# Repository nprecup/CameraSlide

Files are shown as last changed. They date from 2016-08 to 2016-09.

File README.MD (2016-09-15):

Automated Camera Slider
=================================================

The goal of this project is to create a budget, yet high quality, motorized camera slider, with two axis capability, and Bluetooth communications. This slider is to be used in very remote locations for time-lapse landscape astrophotography. This drives a requirement for portability, with a small battery and low power consumption.

Mechanical Design
-----------------------

The slide axis is made using two aluminum shafts that serve as rails. A low cost ACME lead screw moves the cart along the axis, driven by a low cost Futaba S3003 servo modified for continuous rotation. The controller can be adapted (without modification to the circuit) for other mechanical drive systems that may be more practical depending on the resources available, including belts or driven rollers. The choice of using hobby servos instead of stepper motors was made clear by the power consumption and complexity requirement. Complex motion profiles are not necessary, and open loop control will work fine. Stepper motors consume too much current, all the time (though the current can be reduced while not moving). Servo motors already have drivers built into them, making it necessary to supply only power and PWM control input. While the open loop control is based upon dead reckoning (timing), rather than by the advantageous simple steps of a stepper motor, the motors can be moved carefully to produce repeatable results. A stepper motor requires additional drive circuitry, increasing cost and complexity.

Circuit Design
-----------------------

This project uses a BlueGiga BLE112 module to control and interface with a motorized camera slide. The BLE112 module contains a 2541 microcontroller that is capable of providing 16-bit resolution PWM output for servo drive signals, hardware interrupt events for limit switches, and timers with GPIO to trigger a camera shutter for time lapse photography. The system is currently being developed for Canon EOS cameras, with an Android app for bluetooth control.

The circuit was designed using Eagle PCB design software. The schematic and board files are located in the repository and may be ordered through any PCB fab shop that can handle Eagle .brd files. Below is the schematic of the circuit.

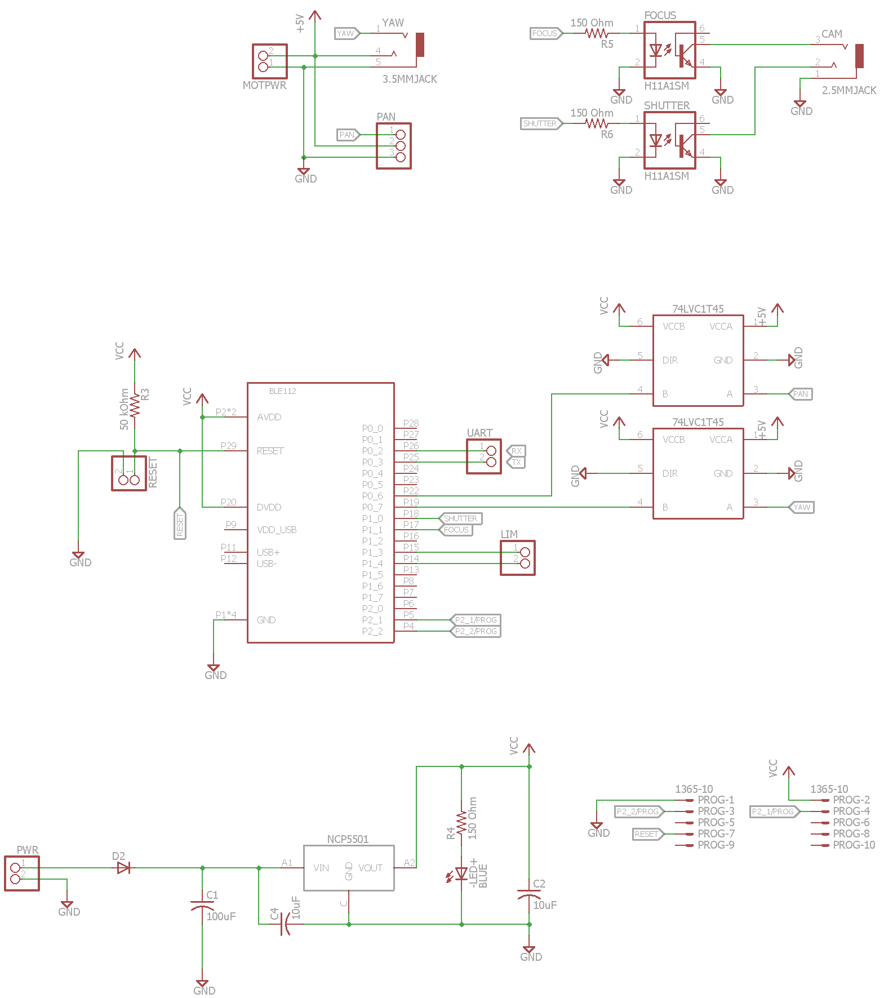
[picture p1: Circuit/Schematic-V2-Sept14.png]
Camaera Slider Circuit


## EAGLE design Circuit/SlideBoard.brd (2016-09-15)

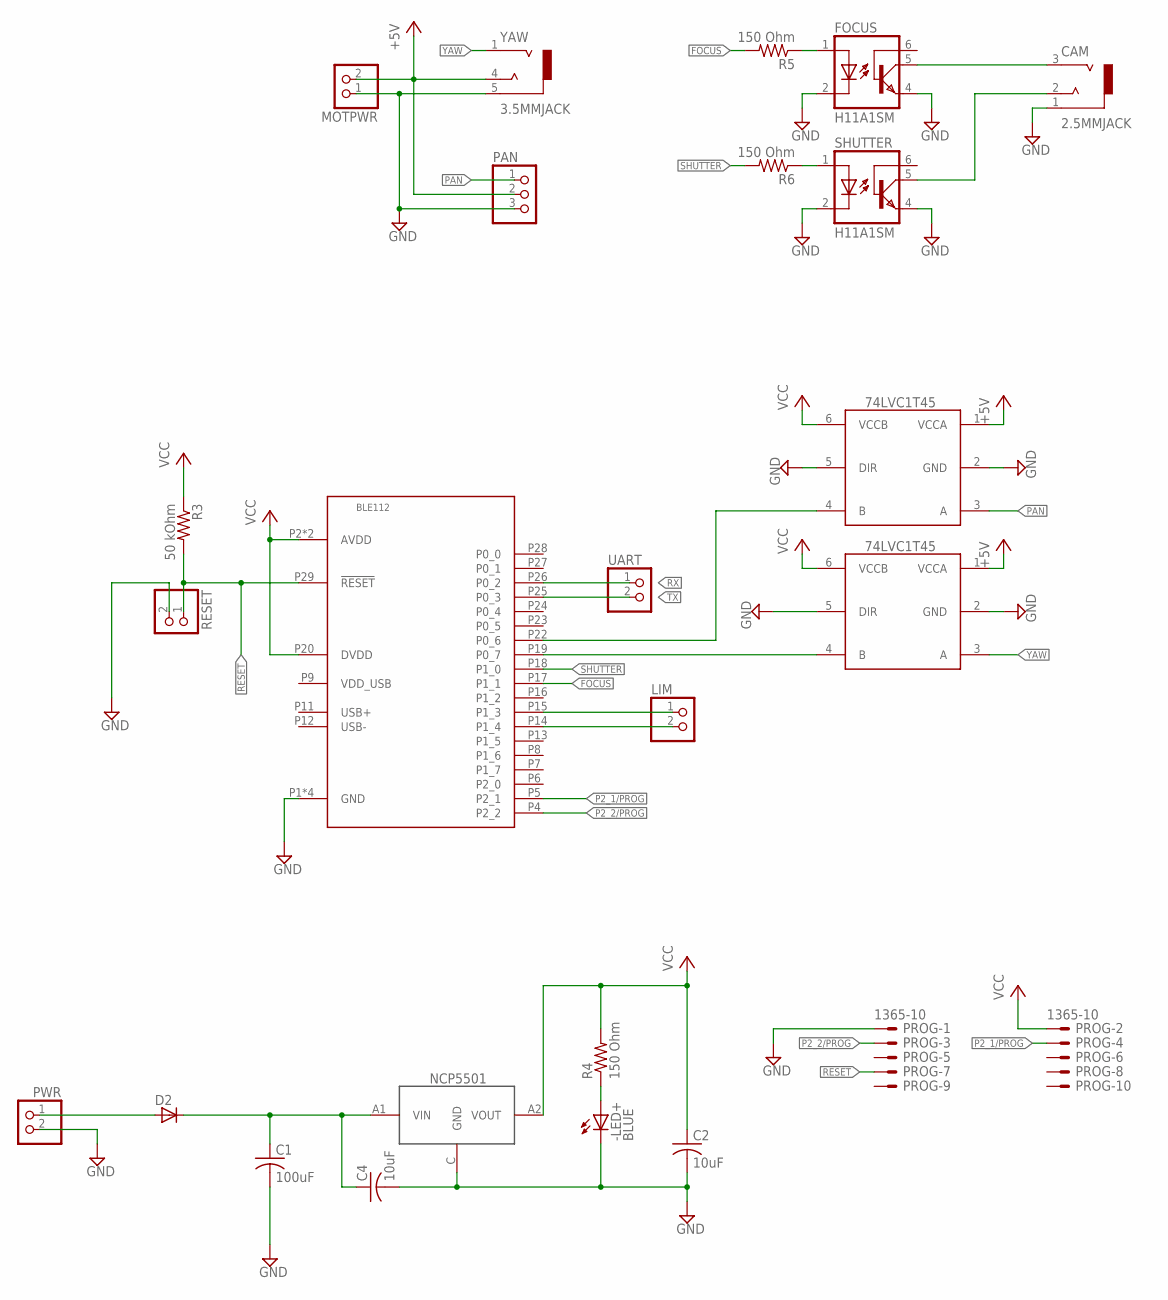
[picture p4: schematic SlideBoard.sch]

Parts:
-LED+: BLUE; CHIP-LED0603
C1: 100uF; C1210
C2, C4: 10uF; C0805
CAM: 2.5MMJACK
D2: D-A1-C3; SOT23
FOCUS: H11A1SM; DIL6-SMD
LIM: PINHD-1X2; 1X02
MOTPWR: PINHD-1X2; 1X02
PAN: PINHD-1X3; 1X03
PROG: 1365-10
PWR: PINHD-1X2; 1X02
R3: 50 kOhm; R0603
R4, R5, R6: 150 Ohm; R0402
RESET: PINHD-1X2; 1X02
SHUTTER: H11A1SM; DIL6-SMD
U$1: BLE112
U$2, U$4: 741T45; SOT363_PHILIPS
U$3: NCP5501; DPACK_3
UART: PINHD-1X2; 1X02
YAW: 3.5MMJACK; 35RA_SMT

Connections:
+5V: MOTPWR.2, PAN.2, U$2.1 (VCCA), U$4.1 (VCCA), YAW.4
FOCUS: R5.2, U$1.P17 (P1_1)
GND: -LED+.C, C1.2, C2.2, C4.2, CAM.1 (5-GND), FOCUS.2 (C), FOCUS.4 (EMI), MOTPWR.1, PAN.3, PROG.1, PWR.2, RESET.2, SHUTTER.2 (C), SHUTTER.4 (EMI), U$1.P1 (GND), U$1.P10 (GND), U$1.P21 (GND), U$1.P30 (GND), U$2.2 (GND), U$2.5 (DIR), U$3.C (GND), U$4.2 (GND), U$4.5 (DIR), YAW.5 (5-GND)
unnamed: D2.1 (A), PWR.1
unnamed: FOCUS.1 (A), R5.1
unnamed: R6.1, SHUTTER.1 (A)
unnamed: CAM.2 (4), SHUTTER.5 (COL)
unnamed: CAM.3 (1), FOCUS.5 (COL)
unnamed: LIM.1, U$1.P15 (P1_3)
unnamed: -LED+.A, R4.1
unnamed: LIM.2, U$1.P14 (P1_4)
unnamed: U$1.P19 (P0_7), U$4.4 (B)
unnamed: C1.1, C4.1, D2.3 (C), U$3.A1 (VIN)
P2_1/PROG: PROG.4, U$1.P5 (P2_1)
P2_2/PROG: PROG.3, U$1.P4 (P2_2)
PAN: PAN.1, U$2.3 (A)
RESET: PROG.7, R3.2, RESET.1, U$1.P29 (!RESET)
RX: U$1.P26 (P0_2), UART.1
SHUTTER: R6.2, U$1.P18 (P1_0)
TX: U$1.P25 (P0_3), UART.2
VCC: C2.1, PROG.2, R3.1, R4.2, U$1.P2 (AVDD), U$1.P3 (AVDD), U$1.P20 (DVDD), U$2.6 (VCCB), U$3.A2 (VOUT), U$4.6 (VCCB)
YAW: U$4.3 (A), YAW.1
YAW_LOW: U$1.P22 (P0_6), U$2.4 (B)

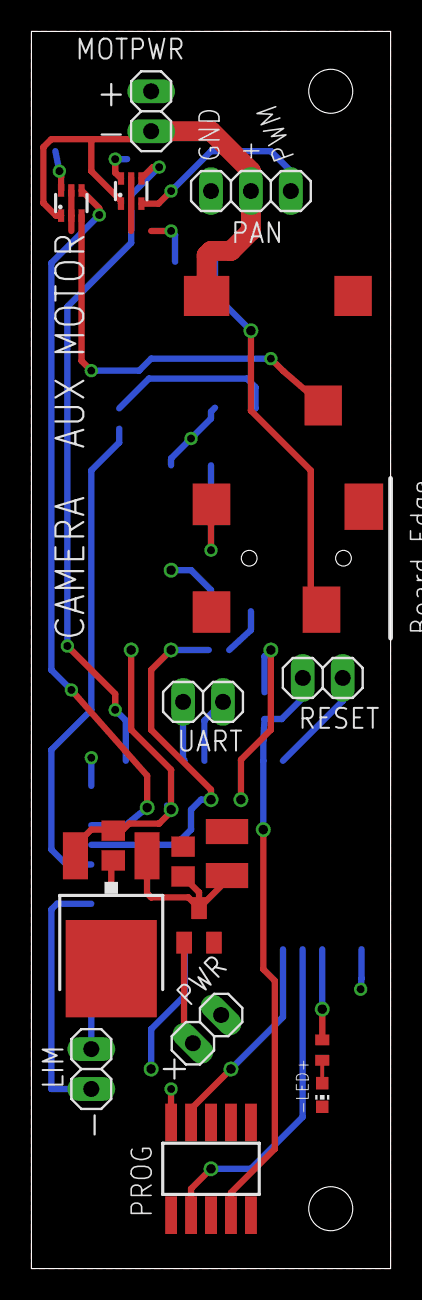
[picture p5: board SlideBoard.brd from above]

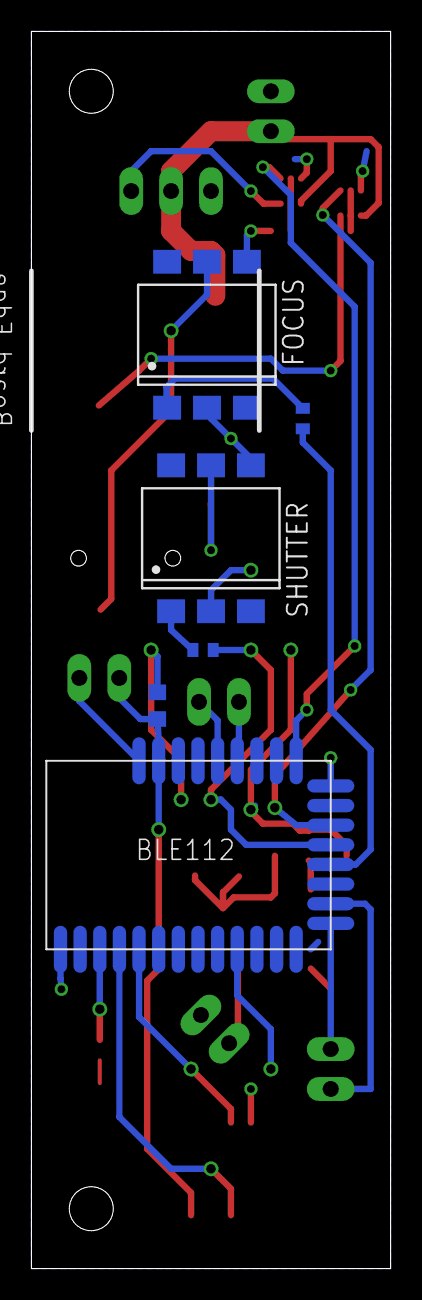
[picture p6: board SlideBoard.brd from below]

Board: 2 copper layers, 22.9 x 78.7 mm, 24 parts (6 on the bottom side), 23 nets.

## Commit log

2016-06-14 Includes schematic
2016-06-15 Added BGScript code files
    [SlideBoard.brd, SlideBoard.sch]
2016-06-15 Updated circuit models to incorporate new changes
2016-06-15 Added to do comment on one-shot timer
2016-06-15 Added translational motion between camera shots
2016-06-15 Changed all interval and exposure management to one-shot timers for accurate timing
2016-06-16 enhanced PWM resolution
2016-06-19 Added servo tuning functionality
2016-06-20 Fixed local errors
    [SlideBoard.brd, SlideBoard.sch]
2016-08-26 Updated controller board to include BLE112 for easier soldering
    [SlideBoard.brd, SlideBoard.sch]
2016-09-13 Fixed missing power connection
    [SlideBoard.brd]
2016-09-15 Updated circuit shematic to reflect current working board version
    [SlideBoard.brd, SlideBoard.sch]
2016-09-15 Updated schematic image file
2016-09-15 removed old schematic
